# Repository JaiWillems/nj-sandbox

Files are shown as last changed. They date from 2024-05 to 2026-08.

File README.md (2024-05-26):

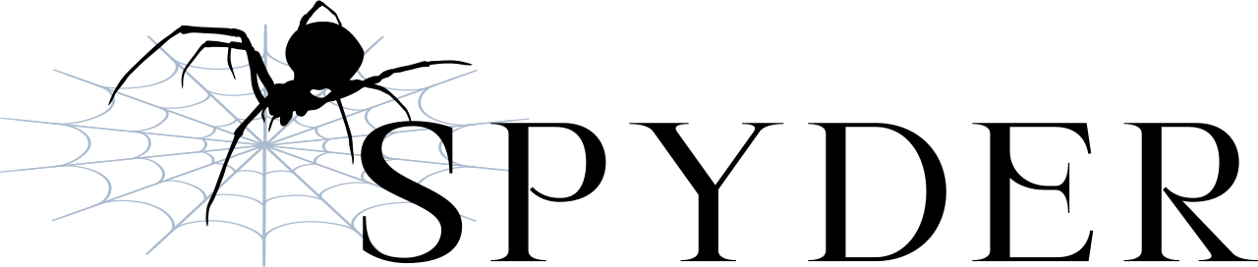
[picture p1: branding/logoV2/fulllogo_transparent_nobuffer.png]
Spyder
# 

NJ-Sandbox is host to the Spyder drone designed by [Nishant Kumar](https://github.com/nishantkumar201) and [Jai Willems](https://github.com/JaiWillems). This repository contains all information related to the drone design necessary to replicate the build, including CAD files, part lists, schematics, and flight code.

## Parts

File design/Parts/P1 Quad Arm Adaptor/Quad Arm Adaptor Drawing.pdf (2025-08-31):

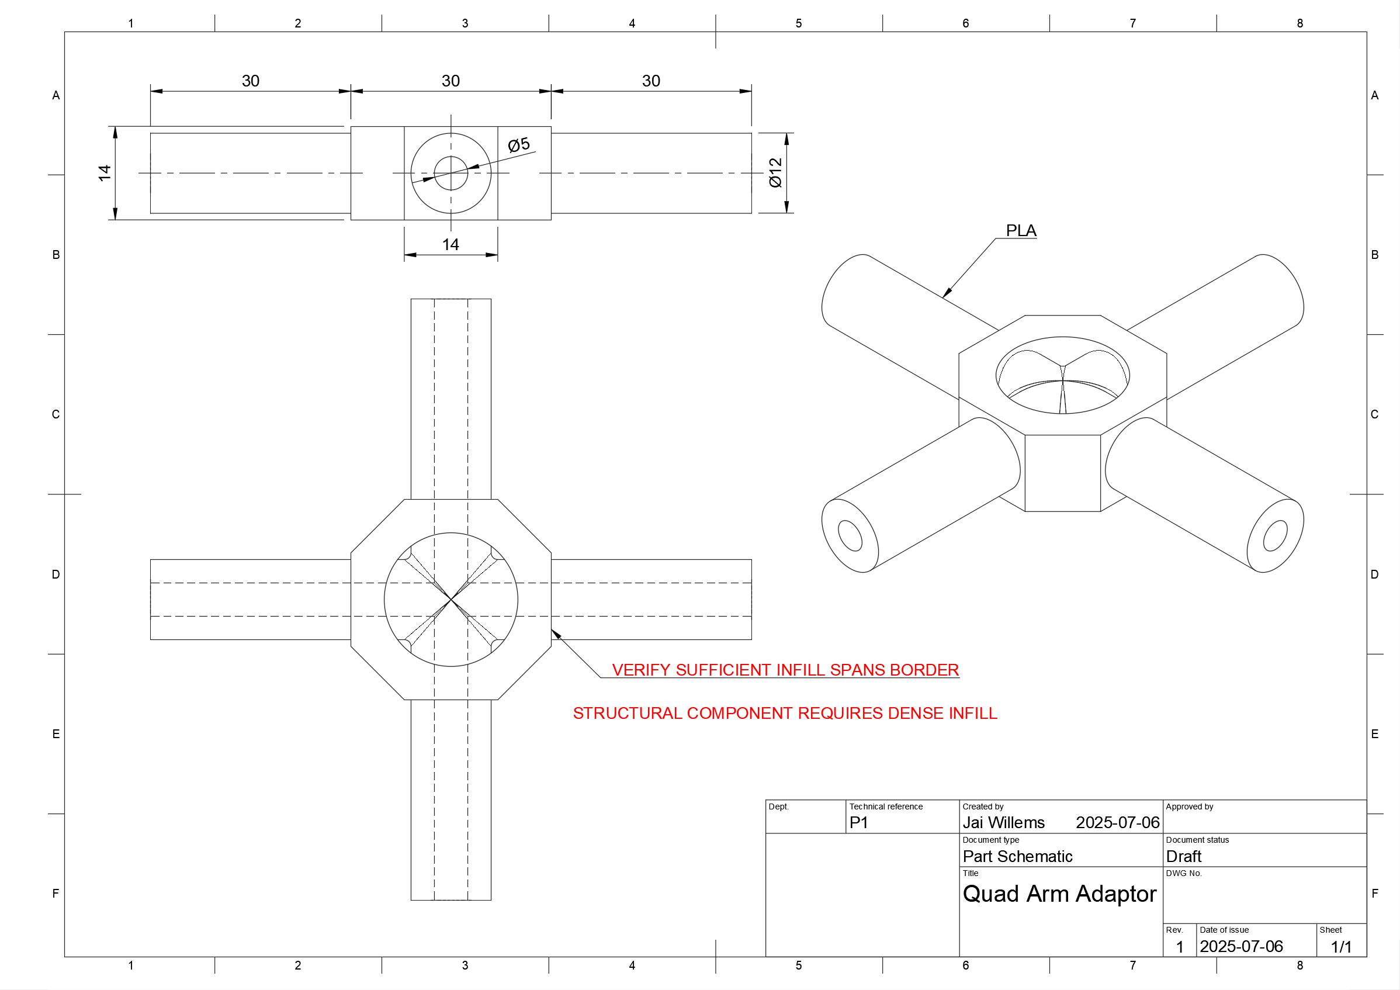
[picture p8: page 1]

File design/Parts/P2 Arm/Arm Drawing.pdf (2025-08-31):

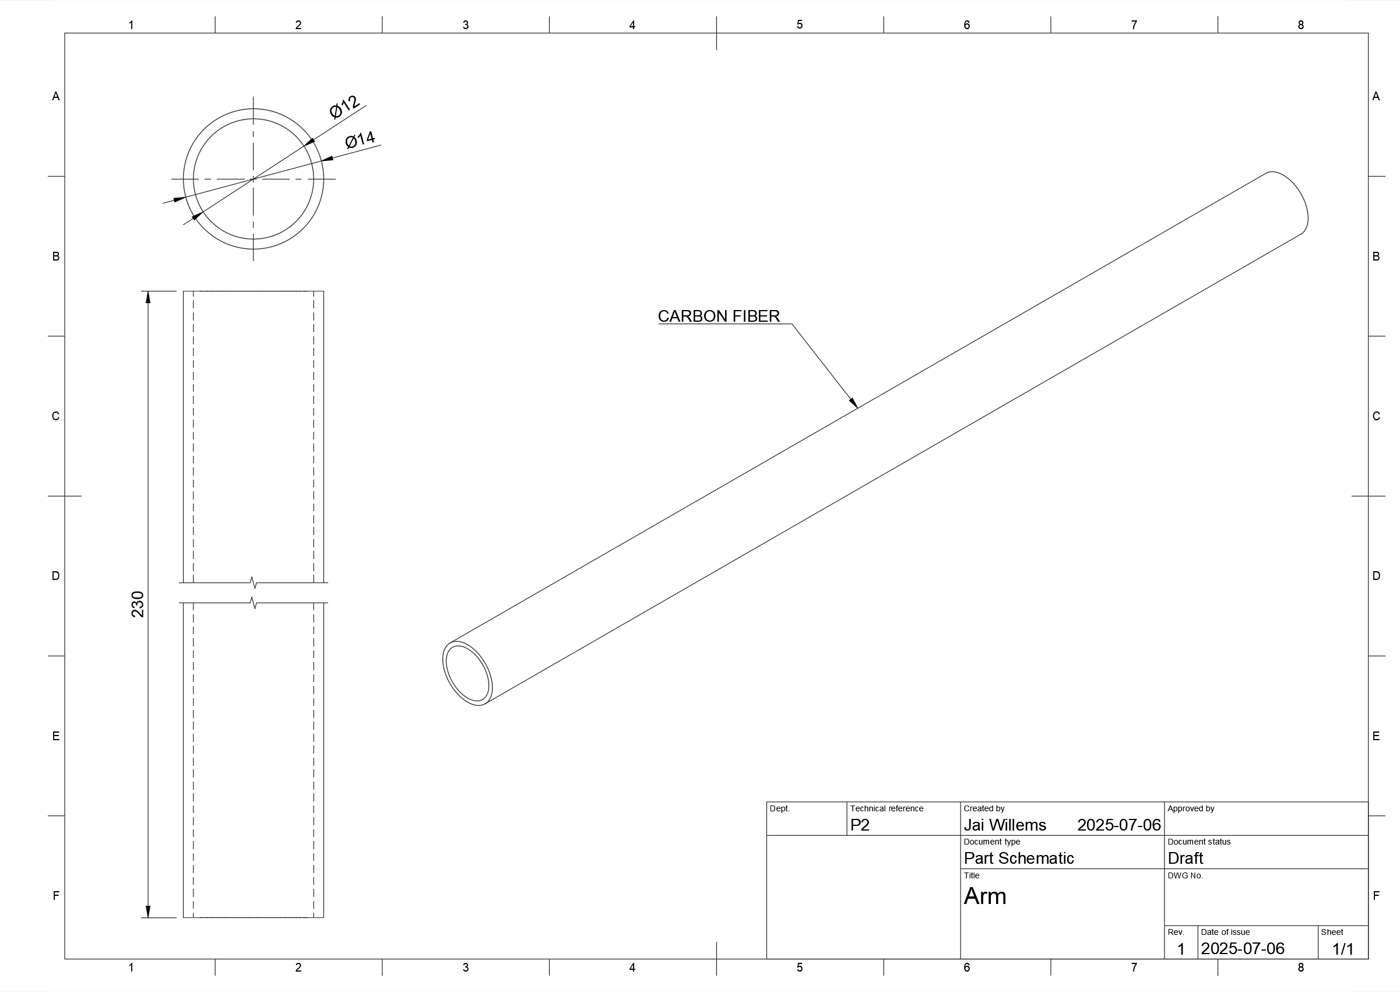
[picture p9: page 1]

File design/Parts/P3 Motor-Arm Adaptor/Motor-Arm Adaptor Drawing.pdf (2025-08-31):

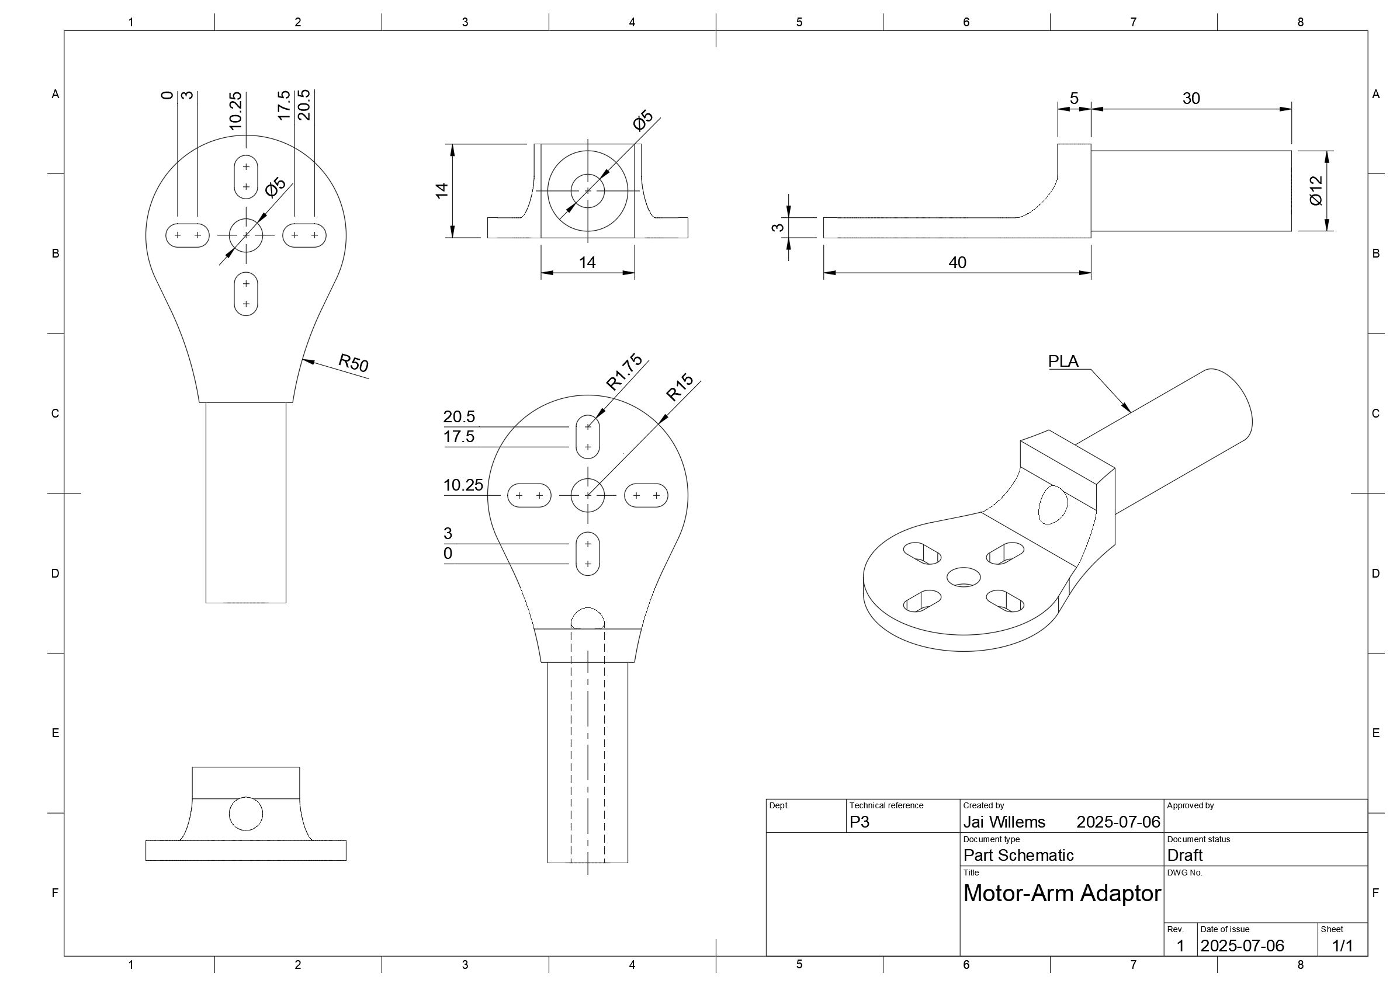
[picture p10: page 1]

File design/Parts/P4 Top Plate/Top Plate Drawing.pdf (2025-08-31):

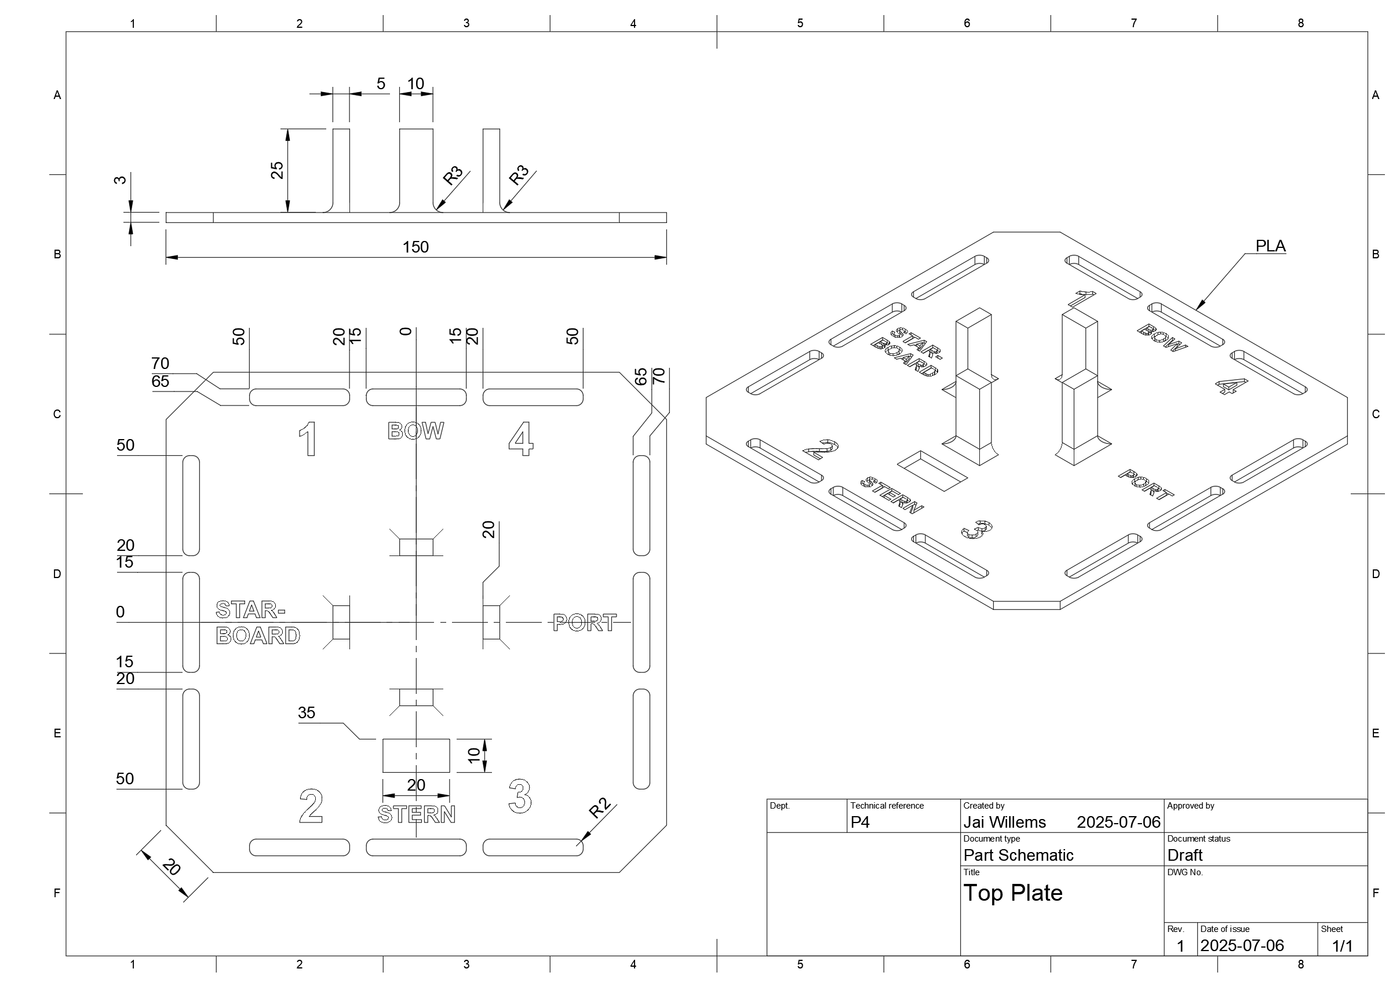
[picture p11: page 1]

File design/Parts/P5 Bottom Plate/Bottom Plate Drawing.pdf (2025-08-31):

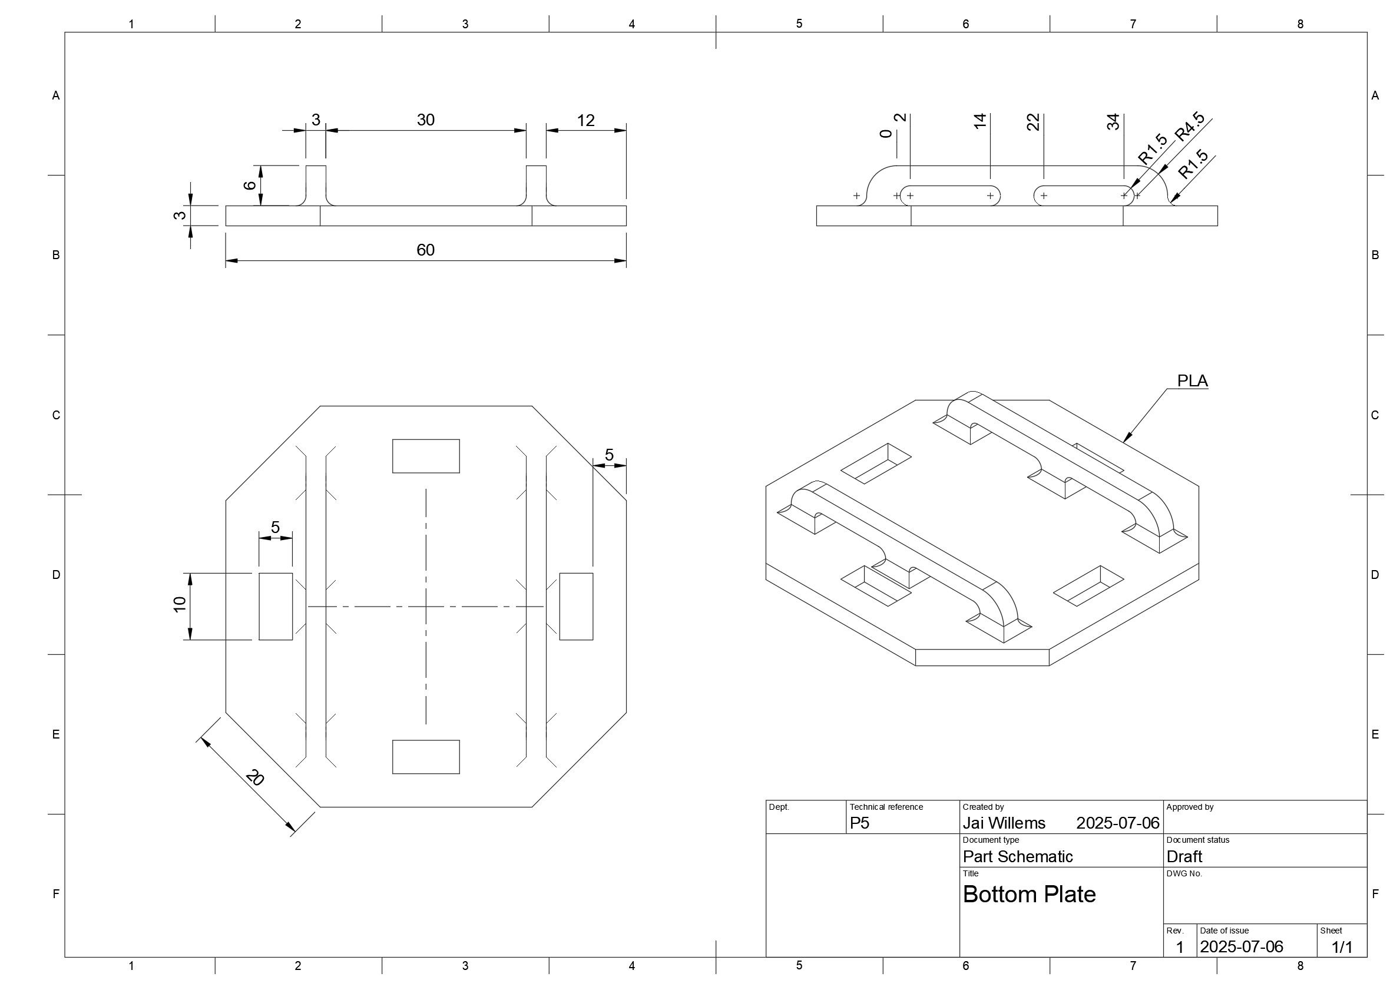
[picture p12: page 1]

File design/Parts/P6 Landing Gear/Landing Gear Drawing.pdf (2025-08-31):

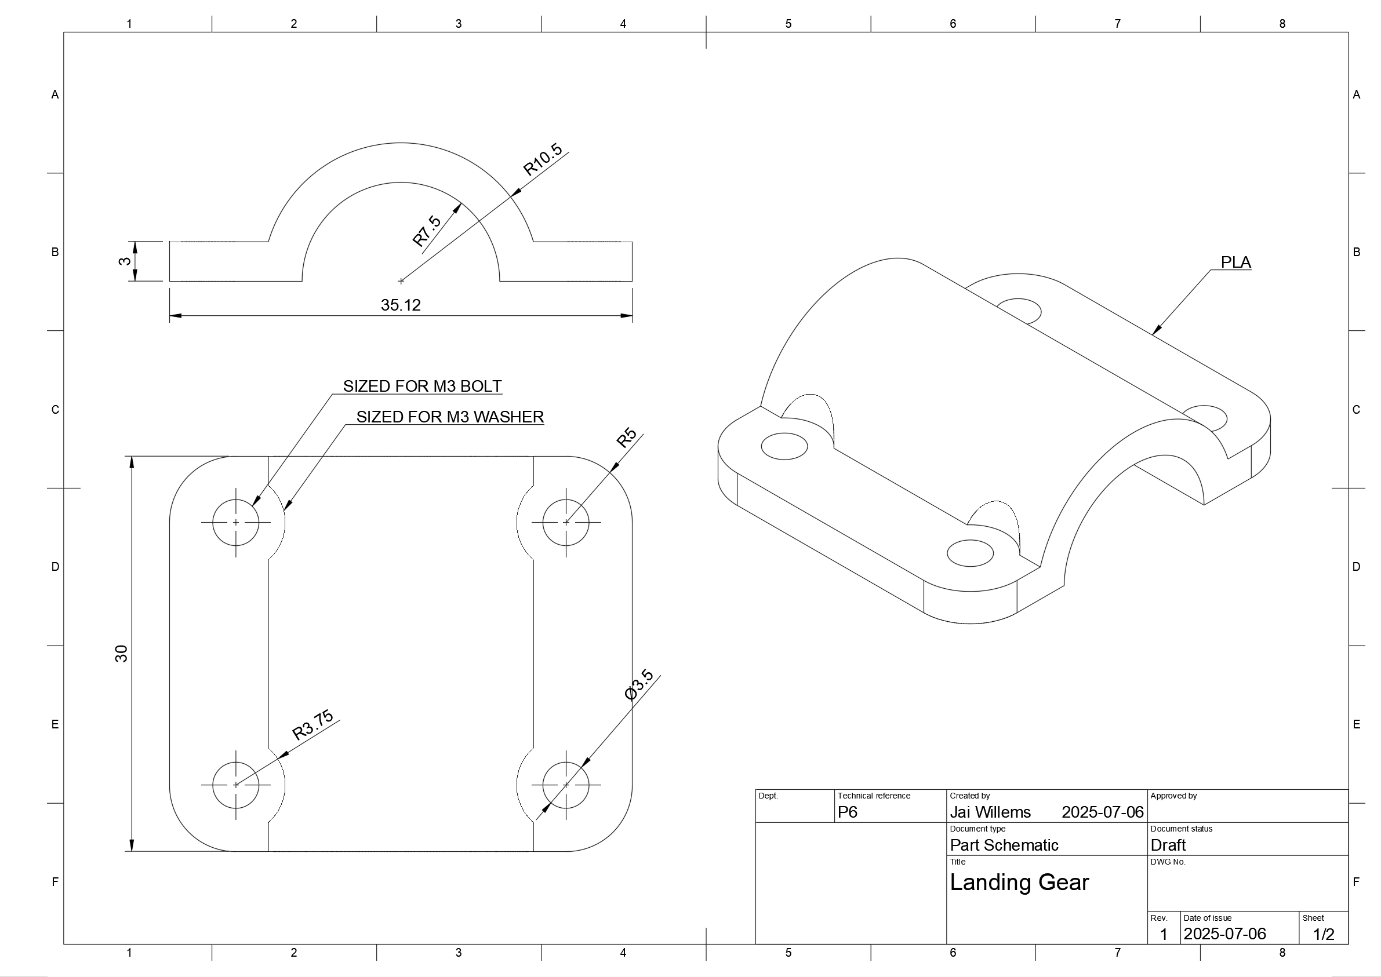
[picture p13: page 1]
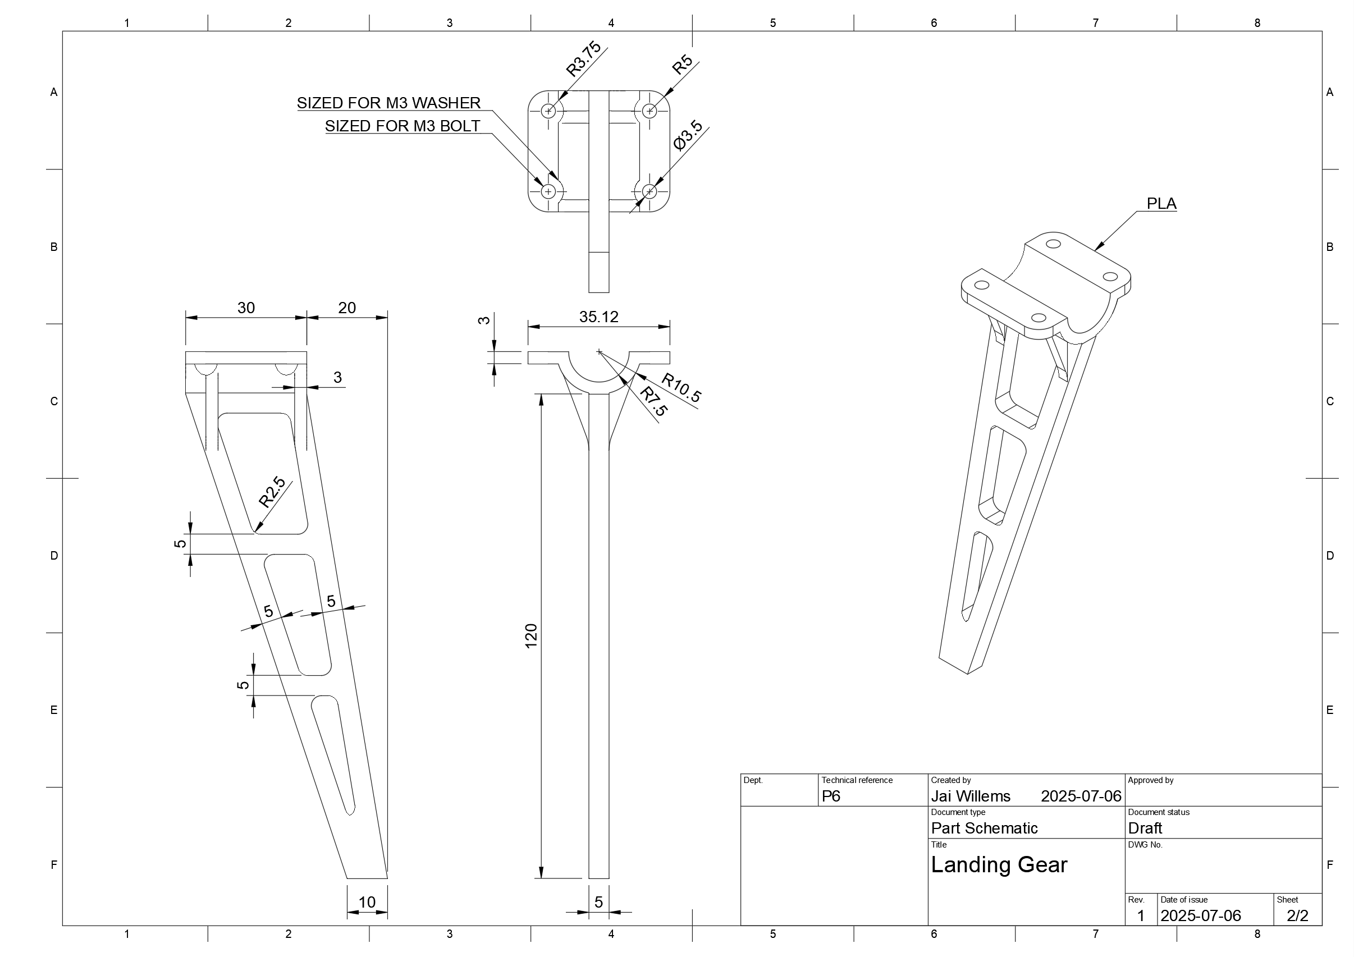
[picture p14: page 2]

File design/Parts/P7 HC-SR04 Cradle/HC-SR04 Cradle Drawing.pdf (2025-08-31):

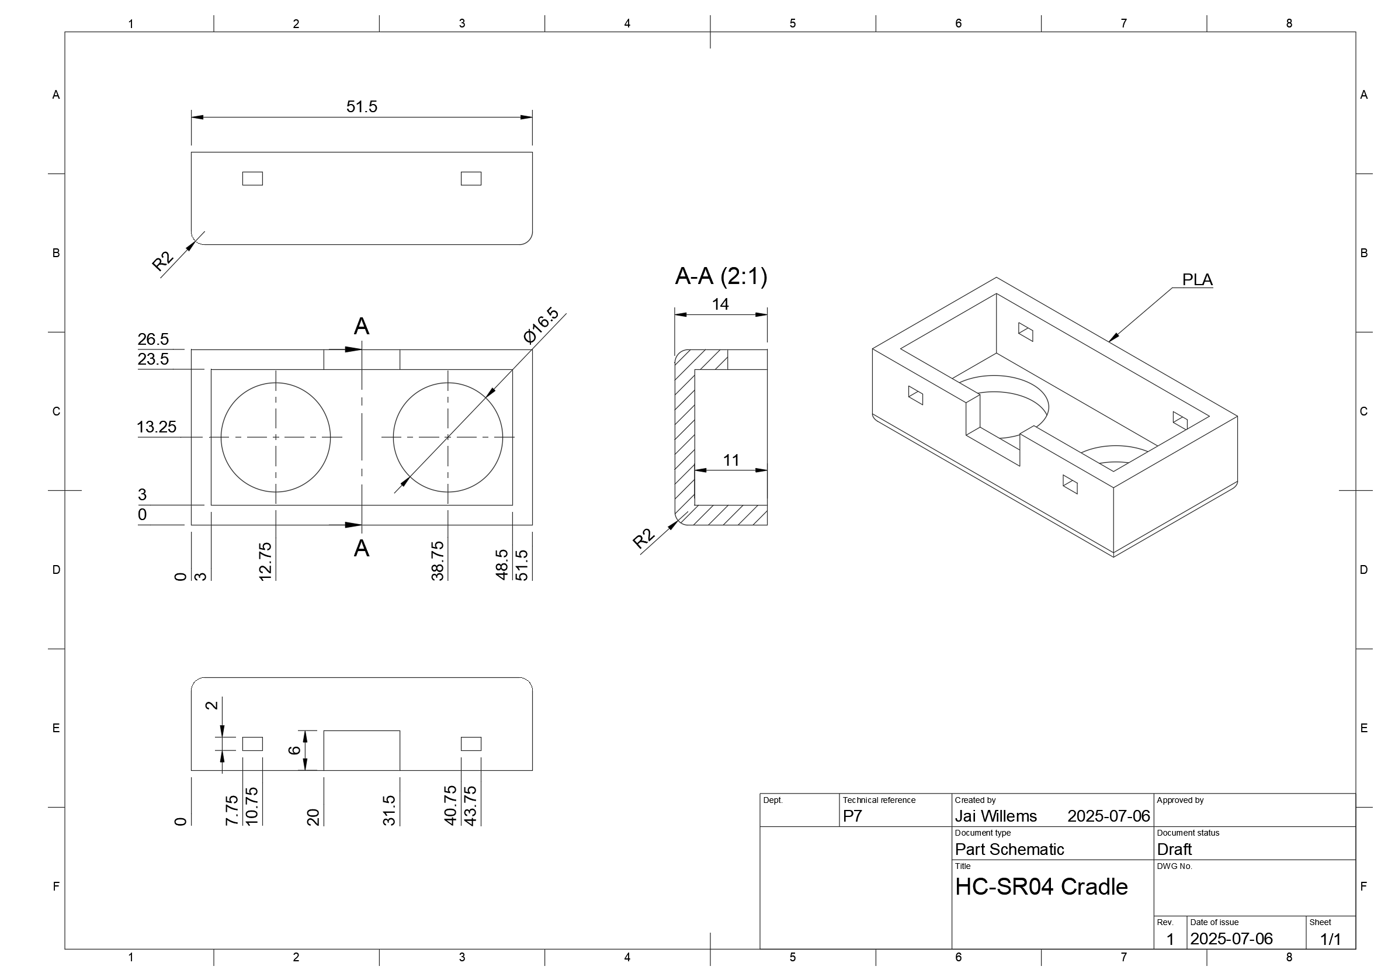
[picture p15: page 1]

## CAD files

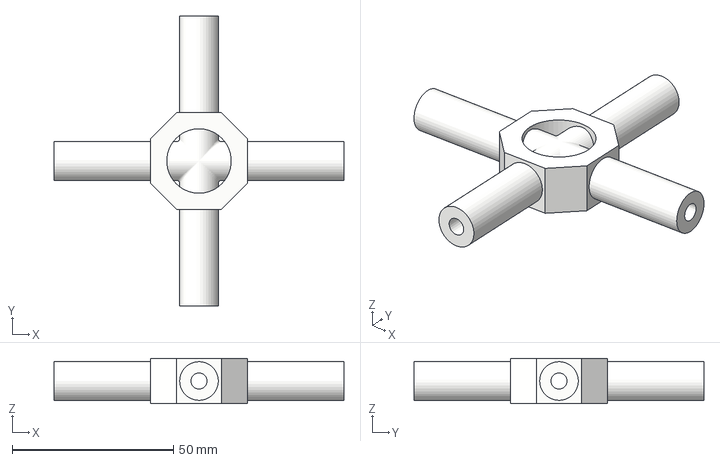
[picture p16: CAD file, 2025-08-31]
design/Parts/P1 Quad Arm Adaptor/Quad Arm Adaptor.3mf
90.0 x 90.0 x 14.0 mm

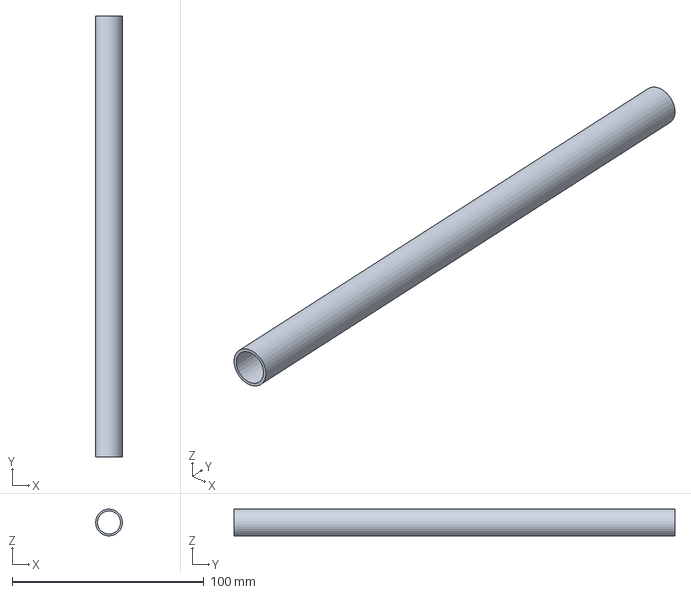
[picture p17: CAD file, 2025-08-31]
design/Parts/P2 Arm/Arm.3mf
14.0 x 230.0 x 14.0 mm

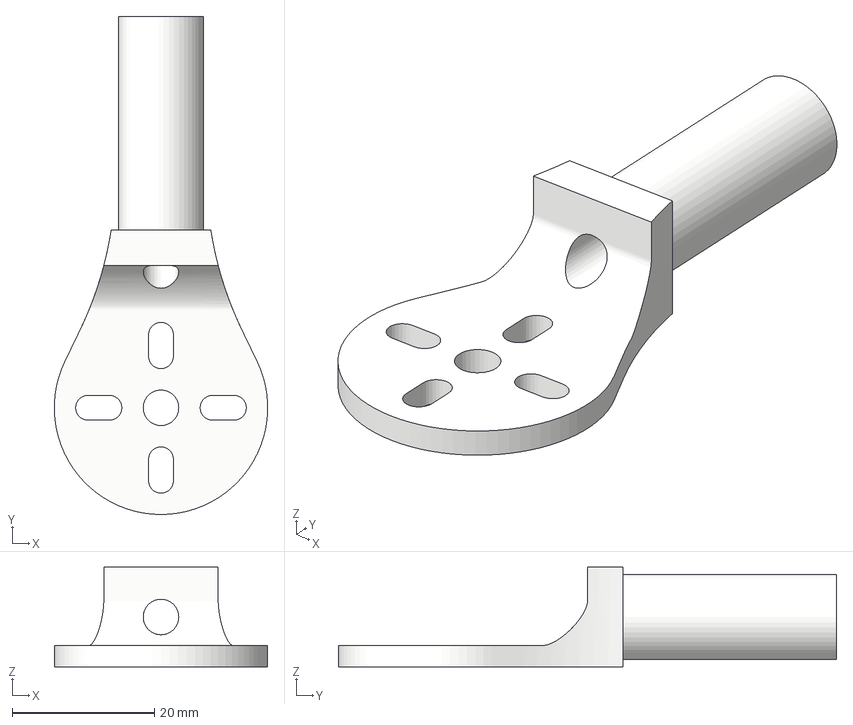
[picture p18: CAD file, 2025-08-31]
design/Parts/P3 Motor-Arm Adaptor/Motor-Arm Adaptor.3mf
30.0 x 70.0 x 14.0 mm

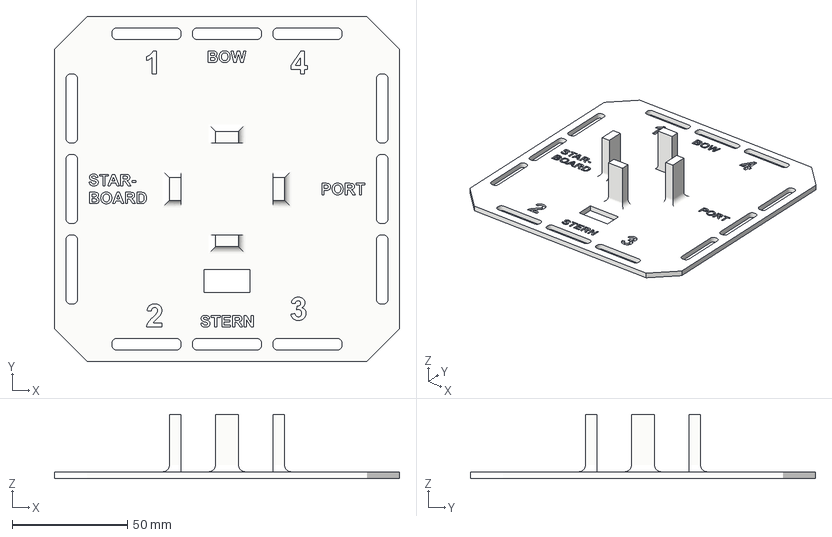
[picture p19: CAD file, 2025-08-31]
design/Parts/P4 Top Plate/Top Plate.3mf
150.0 x 150.0 x 28.0 mm

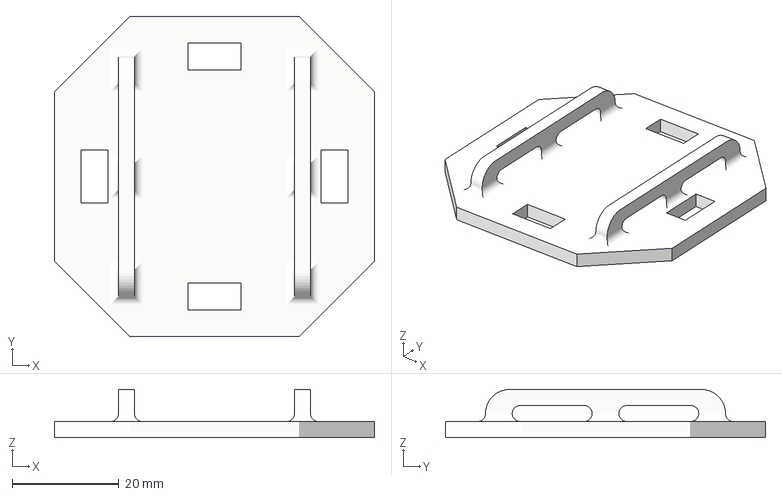
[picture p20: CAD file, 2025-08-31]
design/Parts/P5 Bottom Plate/Bottom Plate.3mf
60.0 x 60.0 x 9.00 mm

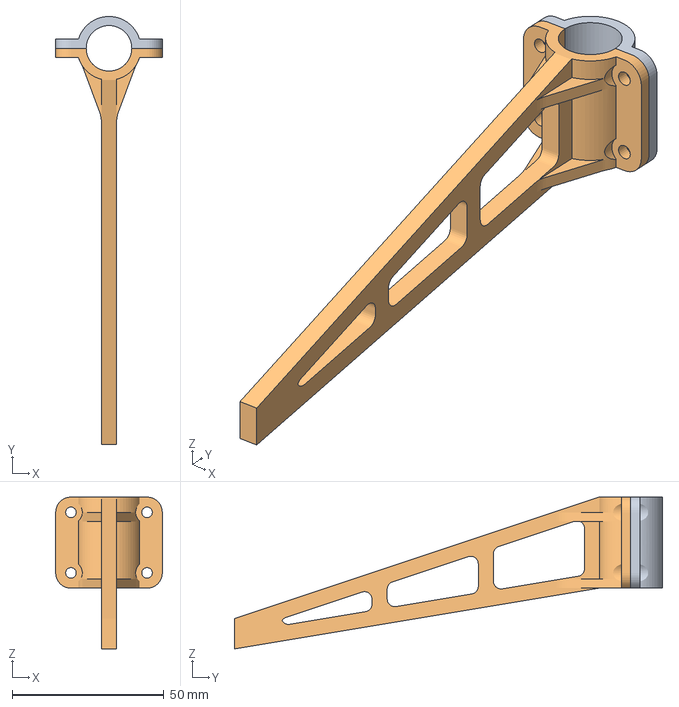
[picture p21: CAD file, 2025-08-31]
design/Parts/P6 Landing Gear/Landing Gear.3mf
35.1 x 141.0 x 50.0 mm

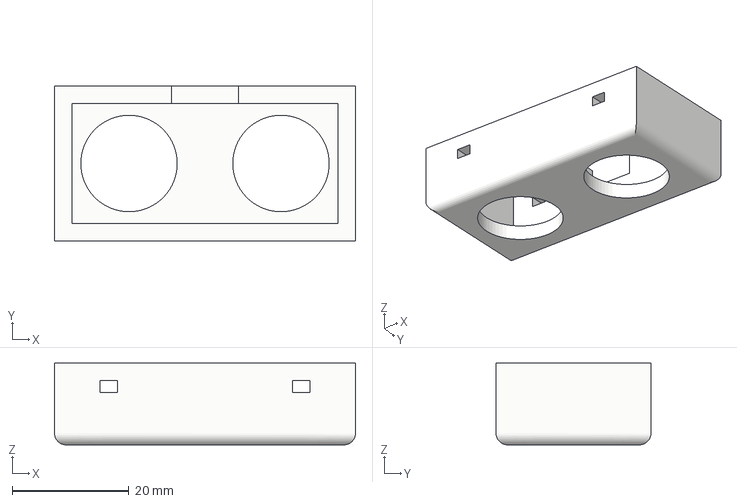
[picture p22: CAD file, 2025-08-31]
design/Parts/P7 HC-SR04 Cradle/HC-SR04 Cradle.3mf
51.5 x 26.5 x 14.0 mm

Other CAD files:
design/Parts/P1 Quad Arm Adaptor/Quad Arm Adaptor.f3d
design/Parts/P2 Arm/Arm.f3d
design/Parts/P3 Motor-Arm Adaptor/Motor-Arm Adaptor.f3d
design/Parts/P4 Top Plate/Top Plate.f3d
design/Parts/P5 Bottom Plate/Bottom Plate.f3d
design/Parts/P6 Landing Gear/Landing Gear.f3d
design/Parts/P7 HC-SR04 Cradle/HC-SR04 Cradle.f3d

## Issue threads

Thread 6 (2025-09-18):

Incorrect ESC Signal Pins in Wiring Schematic

JaiWillems, 2025-09-18:
In the wiring schematic, the pins connected to the control wires for ESC1 and ESC4 should be switched (i.e. D10 -> ESC1, D6 -> ESC4). Wiring of the S1 and S2 platforms assume D10 -> ESC1 and D6 -> ESC4.

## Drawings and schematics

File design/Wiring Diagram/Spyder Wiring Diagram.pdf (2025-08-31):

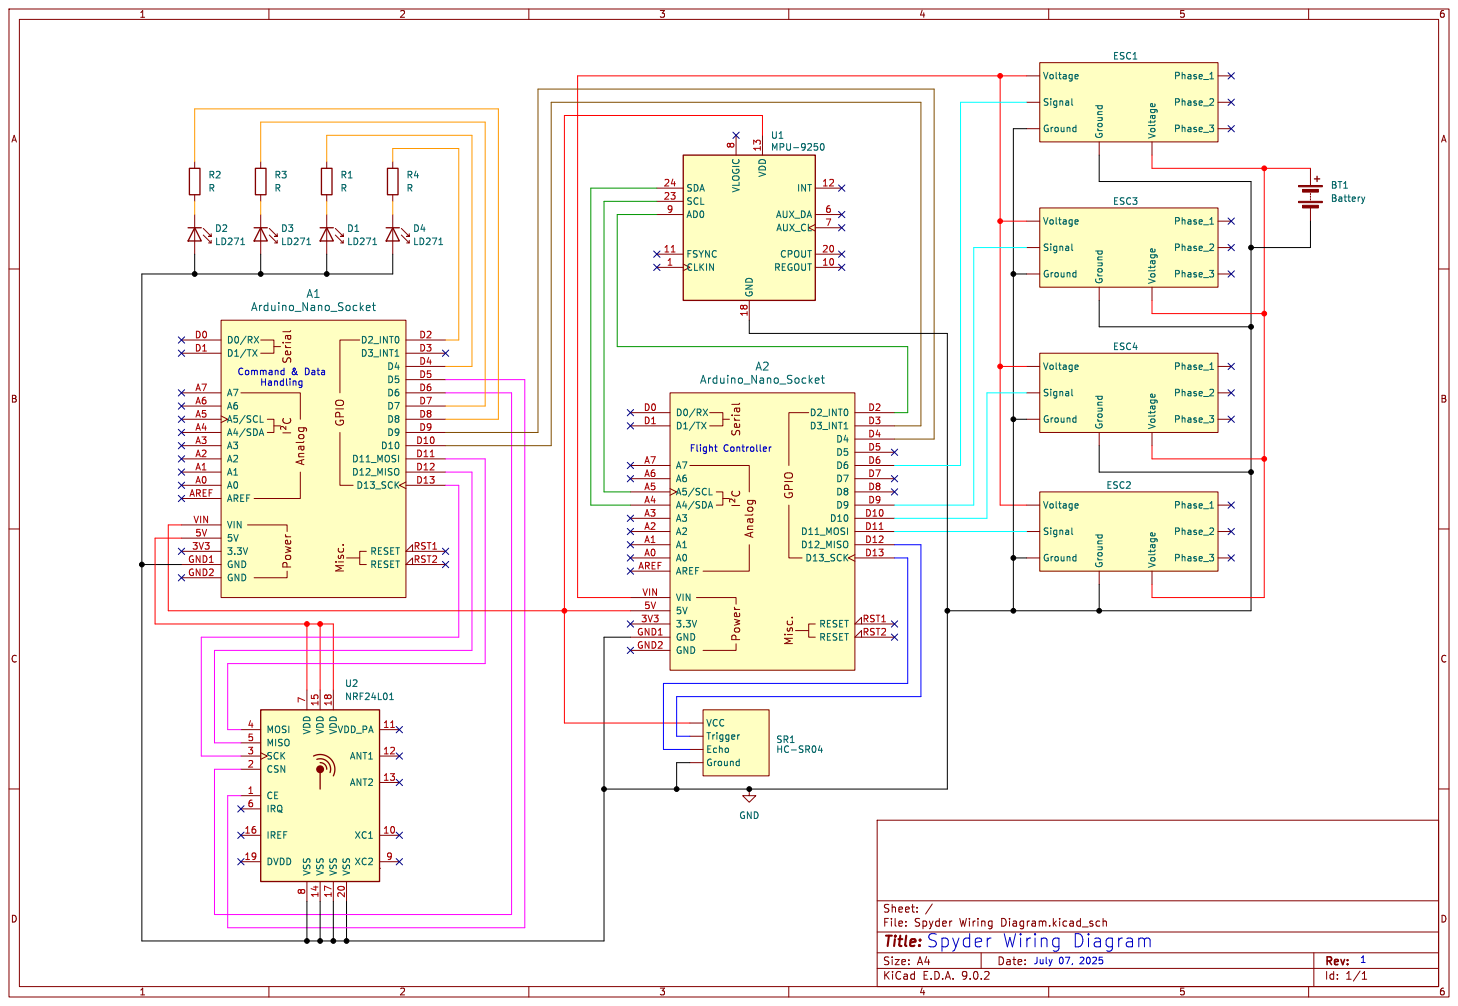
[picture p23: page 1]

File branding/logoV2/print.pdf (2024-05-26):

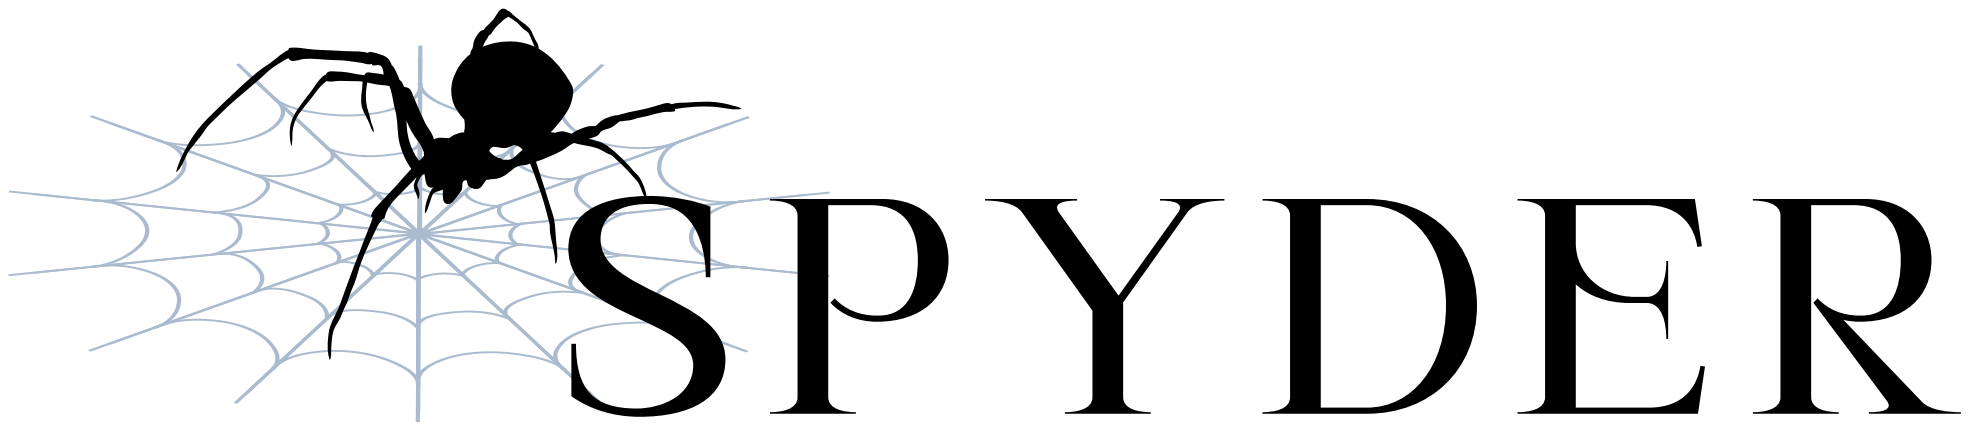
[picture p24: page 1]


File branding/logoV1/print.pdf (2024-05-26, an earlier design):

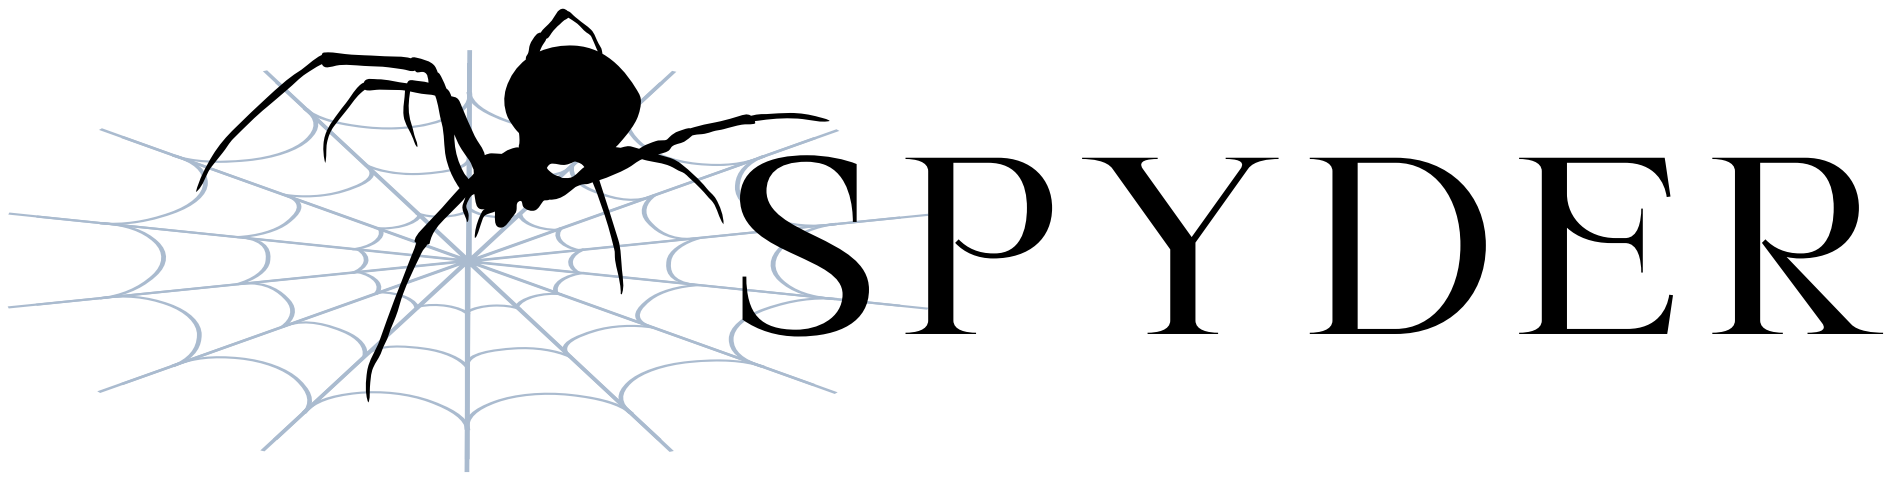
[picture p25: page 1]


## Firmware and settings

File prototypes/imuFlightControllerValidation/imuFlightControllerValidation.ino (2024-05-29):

#include <PIDController.h>
#include <Servo.h>
#include <I2Cdev.h>
#include <MPU6050_6Axis_MotionApps20.h>

// *** DEBUG SETTINGS ***

bool PRINT_IMU_DATA = true;
bool PLOT_RATE_DATA = false;
bool PLOT_ANGLE_DATA = false;
bool PLOT_ANGLE_PID_DATA = false;
bool PRINT_YAW_RATE_PID_INFORMATION = false;
bool PRINT_MOTOR_OUTPUTS = false;

// *** DRONE LEVEL SETTINGS ***

bool STABILIZE_MODE = true;

// *** MOTOR SETTINGS ***

int MIN_ESC_INPUT = 1000;
int MAX_ESC_INPUT = 2000;
int MIN_ESC_INPUT_FROM_PID = -100;
int MAX_ESC_INPUT_FROM_PID = 100;

// *** THROTTLE SETTINGS ***

int MIN_THROTTLE_STICK_POSITION = 0;
int MAX_THROTTLE_STICK_POSITION = 1023;
int MIN_THROTTLE = MIN_ESC_INPUT;
int MAX_THROTTLE = MIN_ESC_INPUT + 0.85 * (MAX_ESC_INPUT - MIN_ESC_INPUT);

// *** ROLL SETTINGS ***

int MIN_ROLL_STICK_POSITION = 0;
int MAX_ROLL_STICK_POSITION = 1023;
int MIN_ROLL_ANGLE_DEG = -60;
int MAX_ROLL_ANGLE_DEG = 60;
int MIN_ROLL_RATE_DEG_PER_SEC = -180;
int MAX_ROLL_RATE_DEG_PER_SEC = 180;

// *** PITCH SETTINGS ***

int MIN_PITCH_STICK_POSITION = 0;
int MAX_PITCH_STICK_POSITION = 1023;
int MIN_PITCH_ANGLE_DEG = -60;
int MAX_PITCH_ANGLE_DEG = 60;
int MIN_PITCH_RATE_DEG_PER_SEC = -180;
int MAX_PITCH_RATE_DEG_PER_SEC = 180;

// *** YAW SETTINGS ***

int MIN_YAW_STICK_POSITION = 0;
int MAX_YAW_STICK_POSITION = 1023;
int MIN_YAW_RATE_DEG_PER_SEC = -180;
int MAX_YAW_RATE_DEG_PER_SEC = 180;

// *** PID SETTINGS ***

int PID_FREQUENCY_HZ = 10;

float ROLL_ANGLE_KP = 1.0;
float ROLL_ANGLE_KI = 0.0;
float ROLL_ANGLE_KD = 0.0;

float PITCH_ANGLE_KP = 1.0;
float PITCH_ANGLE_KI = 0.0;
float PITCH_ANGLE_KD = 0.0;

float ROLL_RATE_KP = 1.0;
float ROLL_RATE_KI = 0.0;
float ROLL_RATE_KD = 0.0;

float PITCH_RATE_KP = 1.0;
float PITCH_RATE_KI = 0.0;
float PITCH_RATE_KD = 0.0;

float YAW_RATE_KP = 1.0;
float YAW_RATE_KI = 0.0;
float YAW_RATE_KD = 0.0;

// *** END OF SETTINGS ***

MPU6050 imu;
int16_t measuredRollRate;
int16_t measuredPitchRate;
int16_t measuredYawRate;
float measuredRollAngle;
float measuredPitchAngle;

PIDController rollAngleController;
PIDController pitchAngleController;
PIDController rollRateController;
PIDController pitchRateController;
PIDController yawRateController;

void setup() {

  Serial.begin(115200);

  imu.initialize();

  if (imu.dmpInitialize() == 0) {
      imu.CalibrateAccel(6);
      imu.CalibrateGyro(6);
      imu.setDMPEnabled(true);
  }
  else {
    Serial.print("DMP Initialization Failed");
  }

  if (STABILIZE_MODE) {
    initializePidController(
      &rollAngleController,
      ROLL_ANGLE_KP,
      ROLL_ANGLE_KI,
      ROLL_ANGLE_KD,
      MIN_ROLL_RATE_DEG_PER_SEC,
      MAX_ROLL_RATE_DEG_PER_SEC
    );
    initializePidController(
      &pitchAngleController,
      PITCH_ANGLE_KP,
      PITCH_ANGLE_KI,
      PITCH_ANGLE_KD,
      MIN_PITCH_RATE_DEG_PER_SEC,
      MAX_PITCH_RATE_DEG_PER_SEC
    );
  }

  initializePidController(
    &rollRateController,
    ROLL_RATE_KP,
    ROLL_RATE_KI,
    ROLL_RATE_KD,
    MIN_ESC_INPUT_FROM_PID,
    MAX_ESC_INPUT_FROM_PID
  );
  initializePidController(
    &pitchRateController,
    PITCH_RATE_KP,
    PITCH_RATE_KI,
    PITCH_RATE_KD,
    MIN_ESC_INPUT_FROM_PID,
    MAX_ESC_INPUT_FROM_PID
  );
  initializePidController(
    &yawRateController,
    YAW_RATE_KP,
    YAW_RATE_KI,
    YAW_RATE_KD,
    MIN_ESC_INPUT_FROM_PID,
    MAX_ESC_INPUT_FROM_PID
  );

  Serial.println("End of Setup");
}

void loop() {

  // Set from CD&H inputs.
  int throttleStickSetting = 512;
  int rollStickSetting = 512;
  int pitchStickSetting = 512;
  int yawStickSetting = 512;

  uint8_t fifoBuffer[64];
  if (imu.dmpGetCurrentFIFOPacket(fifoBuffer)) {

    Quaternion orientation;
    VectorFloat gravity;
    float ypr[3];

    imu.getRotation(
      &measuredRollRate,
      &measuredPitchRate,
      &measuredYawRate
    );

    // Need to negate pitch and yaw rates to get in drone frame.
    measuredPitchRate = -measuredPitchRate;
    measuredYawRate = -measuredYawRate;

    imu.dmpGetQuaternion(
      &orientation,
      fifoBuffer
    );
    imu.dmpGetGravity(
      &gravity,
      &orientation
    );
    imu.dmpGetYawPitchRoll(
      ypr,
      &orientation,
      &gravity
    );

    measuredPitchAngle = ypr[1] * RAD_TO_DEG;
    measuredRollAngle = ypr[2] * RAD_TO_DEG;
  }
  else {
    Serial.println("No IMU Data");
  }

  if (PRINT_IMU_DATA) {
    Serial.print("Pitch:\t"); Serial.print(measuredPitchAngle); Serial.print("\t");
    Serial.print("Roll:\t"); Serial.print(measuredRollAngle); Serial.print("\t");
    Serial.print("Yaw Rate:\t"); Serial.print(measuredYawRate); Serial.print("\t");
    Serial.print("Pitch Rate:\t"); Serial.print(measuredPitchRate); Serial.print("\t");
    Serial.print("Roll Rate:\t"); Serial.println(measuredRollRate);
  }
  if (PLOT_RATE_DATA) {
    Serial.print(measuredYawRate);
    Serial.print(" ");
    Serial.print(measuredPitchRate);
    Serial.print(" ");
    Serial.println(measuredRollRate);
  }
  if (PLOT_ANGLE_DATA) {
    Serial.print(measuredPitchAngle);
    Serial.print(" ");
    Serial.println(measuredRollAngle);
  }

  int throttleContribution = map(
    throttleStickSetting,
    MIN_THROTTLE_STICK_POSITION,
    MAX_THROTTLE_STICK_POSITION,
    MIN_THROTTLE,
    MAX_THROTTLE
  );

  float referenceRollRate;
  if (STABILIZE_MODE) {
    int referenceRollAngle = map(
      rollStickSetting,
      MIN_ROLL_STICK_POSITION,
      MAX_ROLL_STICK_POSITION,
      MIN_ROLL_ANGLE_DEG,
      MAX_ROLL_ANGLE_DEG
    );
    referenceRollRate = computePidIteration(
      &rollAngleController,
      referenceRollAngle,
      measuredRollAngle
    );
    if (PLOT_ANGLE_PID_DATA) {
      Serial.print(referenceRollRate);
      Serial.print(" ");
    }
  }
  else {
    referenceRollRate = map(
      rollStickSetting,
      MIN_ROLL_STICK_POSITION,
      MAX_ROLL_STICK_POSITION,
      MIN_ROLL_RATE_DEG_PER_SEC,
      MAX_ROLL_RATE_DEG_PER_SEC
    );
  }
  float rollContribution = computePidIteration(
    &rollRateController,
    referenceRollRate,
    measuredRollRate
  );

  float referencePitchRate;
  if (STABILIZE_MODE) {
    int referencePitchAngle = map(
      pitchStickSetting,
      MIN_PITCH_STICK_POSITION,
      MAX_PITCH_STICK_POSITION,
      MIN_PITCH_ANGLE_DEG,
      MAX_PITCH_ANGLE_DEG
    );
    referencePitchRate = computePidIteration(
      &pitchAngleController,
      referencePitchAngle,
      measuredPitchAngle
    );
    if (PLOT_ANGLE_PID_DATA) {
      Serial.println(referencePitchRate);
    }
  }
  else {
    referencePitchRate = map(
      pitchStickSetting,
      MIN_PITCH_STICK_POSITION,
      MAX_PITCH_STICK_POSITION,
      MIN_PITCH_RATE_DEG_PER_SEC,
      MAX_PITCH_RATE_DEG_PER_SEC
    );
  }
  float pitchContribution = computePidIteration(
    &pitchRateController,
    referencePitchRate,
    measuredPitchRate
  );

  int referenceYawRate = map(
    yawStickSetting,
    MIN_YAW_STICK_POSITION,
    MAX_YAW_STICK_POSITION,
    MIN_YAW_RATE_DEG_PER_SEC,
    MAX_YAW_RATE_DEG_PER_SEC
  );
  float yawContribution = computePidIteration(
    &yawRateController,
    referenceYawRate,
    measuredYawRate
  );

  if (PRINT_YAW_RATE_PID_INFORMATION) {
    Serial.print("Yaw Contribution:\t"); Serial.print(yawContribution); Serial.print("\t");
    Serial.print("Reference:\t"); Serial.print(referenceYawRate); Serial.print("\t");
    Serial.print("Measured:\t"); Serial.println(measuredYawRate);
  }

  if (PRINT_MOTOR_OUTPUTS) {
    Serial.print("Motor 1: ");
    Serial.print(
      mixMotorInputs(
        true,
        false,
        throttleContribution,
        yawContribution,
        pitchContribution,
        rollContribution
      )
    );
    Serial.print("\t");

    Serial.print("Motor 2: ");
    Serial.print(
      mixMotorInputs(
        false,
        false,
        throttleContribution,
        yawContribution,
        pitchContribution,
        rollContribution
      )
    );
    Serial.print("\t");

    Serial.print("Motor 3: ");
    Serial.print(
      mixMotorInputs(
        false,
        true,
        throttleContribution,
        yawContribution,
        pitchContribution,
        rollContribution
      )
    );
    Serial.print("\t");

    Serial.print("Motor 4: ");
    Serial.print(
      mixMotorInputs(
        true,
        true,
        throttleContribution,
        yawContribution,
        pitchContribution,
        rollContribution
      )
    );
    Serial.print("\t");

    Serial.println();
  }

  delay(1000 / PID_FREQUENCY_HZ);
}

void initializePidController(
  PIDController* pid,
  float kp,
  float ki,
  float kd,
  float minLimit,
  float maxLimit
) {
  (*pid).begin();
  (*pid).tune(kp, ki, kd);
  (*pid).limit(minLimit, maxLimit);
  (*pid).minimize(1);
}

float computePidIteration(
  PIDController* pid,
  float reference,
  float measured
) {
  (*pid).setpoint(reference);
  return (*pid).compute(measured);
}

float mixMotorInputs(
  bool bow,
  bool port,
  float throttle,
  float yaw,
  float pitch,
  float roll
) {
  bool isCcwMotor = (bow && !port) || (!bow && port);

  float motorInput = throttle;
  motorInput = motorInput + ((isCcwMotor) ? yaw : -yaw);
  motorInput = motorInput + ((bow) ? pitch : -pitch);
  motorInput = motorInput + ((port) ? roll : -roll);

  return constrain(
    motorInput,
    MIN_ESC_INPUT,
    MAX_ESC_INPUT
  );
}

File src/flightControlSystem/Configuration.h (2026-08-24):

/*
BSD 3-Clause License

Copyright (c) 2026, Nishant Kumar, Jai Willems

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
1. Redistributions of source code must retain the above copyright notice, this
   list of conditions and the following disclaimer.

2. Redistributions in binary form must reproduce the above copyright notice,
   this list of conditions and the following disclaimer in the documentation
   and/or other materials provided with the distribution.

3. Neither the name of the copyright holder nor the names of its
   contributors may be used to endorse or promote products derived from
   this software without specific prior written permission.

THIS SOFTWARE IS PROVIDED BY THE COPYRIGHT HOLDERS AND CONTRIBUTORS "AS IS"
AND ANY EXPRESS OR IMPLIED WARRANTIES, INCLUDING, BUT NOT LIMITED TO, THE
IMPLIED WARRANTIES OF MERCHANTABILITY AND FITNESS FOR A PARTICULAR PURPOSE ARE
DISCLAIMED. IN NO EVENT SHALL THE COPYRIGHT HOLDER OR CONTRIBUTORS BE LIABLE
FOR ANY DIRECT, INDIRECT, INCIDENTAL, SPECIAL, EXEMPLARY, OR CONSEQUENTIAL
DAMAGES (INCLUDING, BUT NOT LIMITED TO, PROCUREMENT OF SUBSTITUTE GOODS OR
SERVICES; LOSS OF USE, DATA, OR PROFITS; OR BUSINESS INTERRUPTION) HOWEVER
CAUSED AND ON ANY THEORY OF LIABILITY, WHETHER IN CONTRACT, STRICT LIABILITY,
OR TORT (INCLUDING NEGLIGENCE OR OTHERWISE) ARISING IN ANY WAY OUT OF THE USE
OF THIS SOFTWARE, EVEN IF ADVISED OF THE POSSIBILITY OF SUCH DAMAGE.
*/

#ifndef Configuration_h
#define Configuration_h

// *** MOTORS ***

const uint8_t MOTOR_ONE_PIN = 10;
const bool MOTOR_ONE_BOW = true;
const bool MOTOR_ONE_PORT = false;

const uint8_t MOTOR_TWO_PIN = 9;
const bool MOTOR_TWO_BOW = false;
const bool MOTOR_TWO_PORT = false;

const uint8_t MOTOR_THREE_PIN = 11;
const bool MOTOR_THREE_BOW = false;
const bool MOTOR_THREE_PORT = true;

const uint8_t MOTOR_FOUR_PIN = 6;
const bool MOTOR_FOUR_BOW = true;
const bool MOTOR_FOUR_PORT = true;

const uint16_t MOTOR_ARM_TIME = 5000;

// *** UART ***

const uint8_t UART_RX_PIN = 3;
const uint8_t UART_TX_PIN = 4;
const uint16_t UART_BAUD_RATE = 9600;
const uint8_t START_MARKER = 255;

// *** HC-SR04 SENSOR ***

const uint8_t ULTRASONIC_TRIG_PIN = 12;
const uint8_t ULTRASONIC_ECHO_PIN = 13;

// *** DRONE PROPERTIES ***

const float DRONE_MASS = 1.00;
const float ARM_LENGTH = 0.27305; // [m].

#endif

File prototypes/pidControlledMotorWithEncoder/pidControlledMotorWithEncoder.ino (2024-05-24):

#include <util/atomic.h>
#include <PIDController.h>

#define ENC_A_PIN 3
#define ENC_B_PIN 2
#define MOTOR_PWM_PIN 5
#define IN1_PIN 8
#define IN2_PIN 7

PIDController pid;

float KP = 4;
float KD = 0.025;
float KI = 0.025;

volatile int positionCounter = 0;
long previousTime = 0;

void setup() {
  Serial.begin(9600);
  
  pinMode(ENC_A_PIN, INPUT);
  pinMode(ENC_B_PIN, INPUT);
  pinMode(MOTOR_PWM_PIN, OUTPUT);
  pinMode(IN1_PIN, OUTPUT);
  pinMode(IN2_PIN, OUTPUT);

  attachInterrupt(
    digitalPinToInterrupt(ENC_A_PIN),
    readEncoder,
    RISING
  );

  pid.begin();
  pid.tune(KP, KI, KD);
  pid.limit(-255, 255);
  pid.minimize(1);
}

void loop() {
  
  int setpoint = 250 * sin(previousTime / 1e6);
  pid.setpoint(setpoint);

  int position = 0;
  ATOMIC_BLOCK(ATOMIC_RESTORESTATE) {
    position = positionCounter;
  }
  setMotor(
    pid.compute(position),
    MOTOR_PWM_PIN,
    IN1_PIN,
    IN2_PIN
  );

  Serial.print(setpoint);
  Serial.print(" ");
  Serial.print(position);
  Serial.println();

  previousTime = micros();
}

void setMotor(int pwmVal, int pwmPin, int in1Pin, int in2Pin) {
  analogWrite(pwmPin, fabs(pwmVal));
  if (pwmVal > 0) {
    digitalWrite(in1Pin, LOW);
    digitalWrite(in2Pin, HIGH);
  }
  else {
    digitalWrite(in1Pin, HIGH);
    digitalWrite(in2Pin, LOW);
  }
}

void readEncoder() {
  int b = digitalRead(ENC_B_PIN);
  if (b > 0) {
    positionCounter++;
  }
  else {
    positionCounter--;
  }
}

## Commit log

2024-04-27 Add potentiometer controlled esc prototype.
2024-04-27 Add prototype file to seperate folder.
2024-05-12 Add preliminary drone CAD.
    [arm.SLDPRT, bottom_plate.SLDPRT, drone.SLDASM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]
2024-05-24 Update CAD files.
    [arm.SLDPRT, bottom_plate.SLDPRT, drone.SLDASM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]
2024-05-24 Adding and modifying prototype files.
2024-05-24 Remove pid minimizer for plant inputs of reasonable maginutude.
2024-05-24 Rename prototype files for consistency.
2024-05-26 Handle drone frame definition and PID bugs in the flight controller.
2024-05-26 Use constrain function for limiting esc inputs.
2024-05-26 Add flight controller validation prototype code.
2024-05-26 Fix zero bug in flight controller motor mixing function.
2024-05-26 Add preliminary ground station code.
2024-05-26 Resolve wireless communication bugs.
    [commandDataHandling.ino, groundStation.ino]
2024-05-26 uART communication added to CD&H
2024-05-26 Add uART communication on flight controller.
2024-05-27 Add software serial receiver prototype code.
2024-05-27 Resolve IMU/DMP initialization failures.
2024-05-28 Move motor functionality to separate class.
2024-05-29 Create PID interface.
2024-05-29 Extract out imu code.
2024-05-29 Move motor initialization to method.
2024-05-29 Update and rename motor.cpp to Motor.cpp
2024-05-31 Added Altitude PID controller
2024-05-31 Redid the inputs of the throttle PID controller
2024-06-02 Implement our own pid controller.
2024-06-02 Tested Motor class code.
2024-06-02 Change motor control to use writeMicrosectonds.
2024-06-02 Set motor inputs high at attachment to prevent premature arming.
    [Motor.cpp]
2024-06-02 Define ultrasonic class.
2024-06-04 Update CDH and ground station to use ControlCommands class.
2024-06-05 Adding joystick module, spi transmitter, uartCommunication code to prototypes
2024-06-06 Adding spi Communciation Receiver
2024-06-06 Add method to evaluate PID controller with measured derivative.
2024-06-07 Add off, landing, and takeoff flight modes to flight controller.
2025-03-18 Adding electrical schematic
    [Drone Schematic V1.kicad_pcb, Drone Schematic V1.kicad_sch]
2025-07-06 Update wiring diagram with S2 developments.
    [Sheet Format.kicad_pcb, Spyder Wiring Diagram.kicad_sch]
2025-07-06 Move to f3d CAD files and add drawings.
    [Arm.3mf, Arm.f3d, Bottom Plate.3mf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]
2025-09-12 Move wiring diagrams to design artifacts folder.
    [Sheet Format.kicad_pcb, Spyder Wiring Diagram.kicad_sch]
2025-09-12 Change folder name to conform to naming convention.
    [Arm.3mf, Arm.f3d, Bottom Plate.3mf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]
2025-09-18 Remove unnecessary motor inputs.
2025-09-21 Update uart communications class for small bug fixes.
    [UartCommunications.cpp, commandDataHandling.ino, groundStation.ino]
2025-09-29 Add control mapping to the ground station.
    [Configuration.h]
2025-09-29 Refactor out configuration, settings, and types from CDH.
    [Configuration.h]
2025-10-01 Add blinking navigation light capability.
    [Configuration.h]
2025-10-01 Increase CDH type specificity.
    [Configuration.h]
2025-10-01 Increase GS type specificity.
    [Configuration.h]
2025-10-01 Change tab spacing.
    [Configuration.h]
2025-10-02 Move FCS hardware variables to Configuration file.
    [Configuration.h]
2025-10-05 Refactor out uart class for CDH.
2025-10-08 Add bi-directional UART communications.
2025-10-08 Make uart communications code generic.
2025-10-08 Handle uart overflow error by draining buffer.
    [UartCommunications.cpp]
2025-10-11 Add basic ultrasonic files.
2025-10-11 Resolve ultrasonic bug.
2025-10-11 Calibration Ultrasonic bug resolved
    [flightControlSystem.ino]
2025-10-12 Resolve ultrasonic delay issue.
    [Ultrasonic.cpp, flightControlSystem.ino, ultrasonicTest.ino]
2025-10-19 Resolve merge related bugs.
    [flightControlSystem.ino]
2026-03-27 Add signal calibration.
    [Configuration.h]
2026-03-28 Toggle drone state from groundstation.
    [Configuration.h]
2026-04-03 Resolve ground station code syntax error.
    [groundStation.ino]
2026-04-03 Update uart communications to align with cdh data packet.
2026-04-03 Switched SoftwareSerial to NeoSoftSerial and typecasted value correctly
    [UartCommunications.cpp, flightControlSystem.ino]
2026-04-18 Update motor PWM units.
2026-04-25 Rename types and add hover offset.
    [Configuration.h]
2026-04-25 Fix ground station control coordinate systems and update nomenclature.
    [groundStation.ino]
2026-04-26 Add flight inputs to motor PWM conversion (moto un-mixing)!
    [Configuration.h]
2026-04-26 Constrain PWM duty cycle in Motor class.
2026-05-04 Resolve PID noise error and motor arming.
    [Motor.cpp, flightControlSystem.ino]
